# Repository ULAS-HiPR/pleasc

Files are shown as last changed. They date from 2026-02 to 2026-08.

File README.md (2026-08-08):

# Pléasc

Pléasc is the recovery-deployment node in [Ogma](https://sean-osullivan.com/projects/ogma/), the University of Limerick Aeronautics Society's modular avionics stack for high-powered rocketry.

## Role

- Monitors continuity on four deployment channels.
- Controls four recovery outputs from an STM32F072.
- Uses guarded arm and fire commands over the 500 kbit/s CAN bus.
- Keeps recovery outputs in defined safe states unless the complete command path is valid.

## Repository

- `hardware/` - KiCad design and manufacturing outputs.
- `firmware/` - embedded firmware, continuity/deployment probes, and tests.

## Status

Rev 1 firmware and hardware bring-up continue on [`ogma/flight-hardening`](https://github.com/ULAS-HiPR/pleasc/tree/ogma/flight-hardening). Release-candidate firmware builds and software tests pass, but hardware-in-the-loop validation is still underway. Pléasc is not yet flight-proven.

## Manufacturing support

Rev 1 PCB fabrication was sponsored through [EasyEDA Education](https://easyeda.com/education) and manufactured by [JLCPCB](https://jlcpcb.com/). The board was designed in KiCad and imported into EasyEDA Pro for the sponsorship and manufacturing workflow.

## More information

See the [Ogma project write-up](https://sean-osullivan.com/projects/ogma/) for the complete stack, bring-up work, and current status.

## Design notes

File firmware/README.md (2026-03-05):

# Lamh

Lamh is for any active control like airbrakes or canards. It will control servos.

## Set-Up

```bash
git clone git@github.com:ULAS-HiPR/pleasc.git
cd lamh
git submodule update --init --recursive
```

## Libraries used:

### From Braiteoiri:

- Servo
- LED

### From Comheadan:

- CAN
- PWM

### Other:

- FreeRTOS

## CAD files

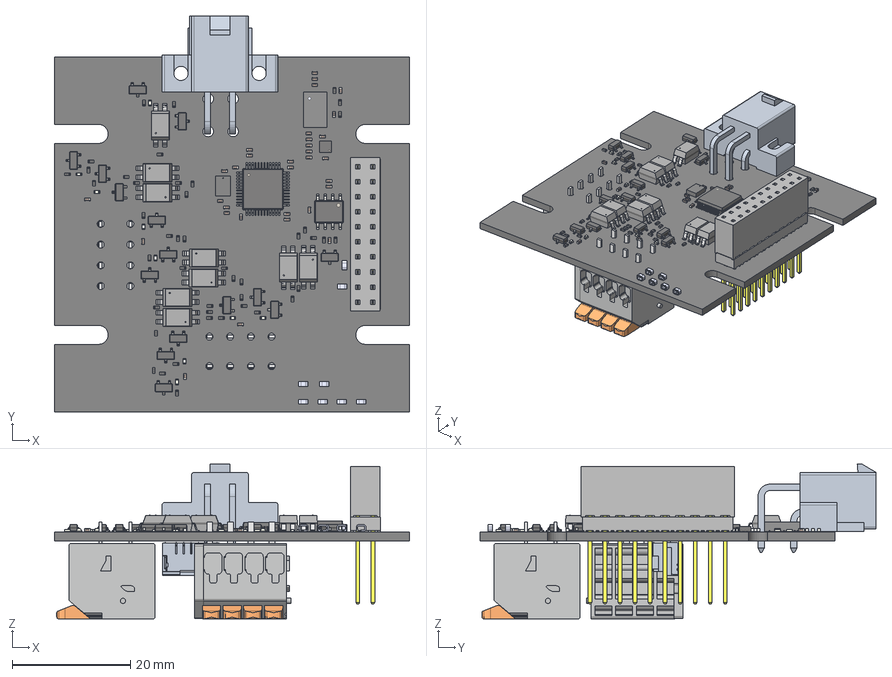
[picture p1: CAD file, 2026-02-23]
hardware/Pleasc.step
60.0 x 66.9 x 26.1 mm
C_0402_1005Metric x 32
S2761-46R x 8
R_0402_1005Metric x 44
SOT-23 x 15
LTV-817S x 9
LED_0402_1005Metric x 9
SOIC-8_3.9x4.9mm_P1.27mm
MPM3650CGQW
WSON-6-1EP_2x2mm_P0.65mm_EP1x1.6mm
ESQ-110-14-G-D-LL_socket
ESQ-110-14-G-D-LL_pins
ESQ-110-14-G-D-LL2_pins
ESQ-110-14-G-D-LL_bpins
LQFP-48_7x7mm_P0.5mm
XTAL_NX3225GD-8MHZ-STD-CRA-3_NDK
Pleasc_PCB

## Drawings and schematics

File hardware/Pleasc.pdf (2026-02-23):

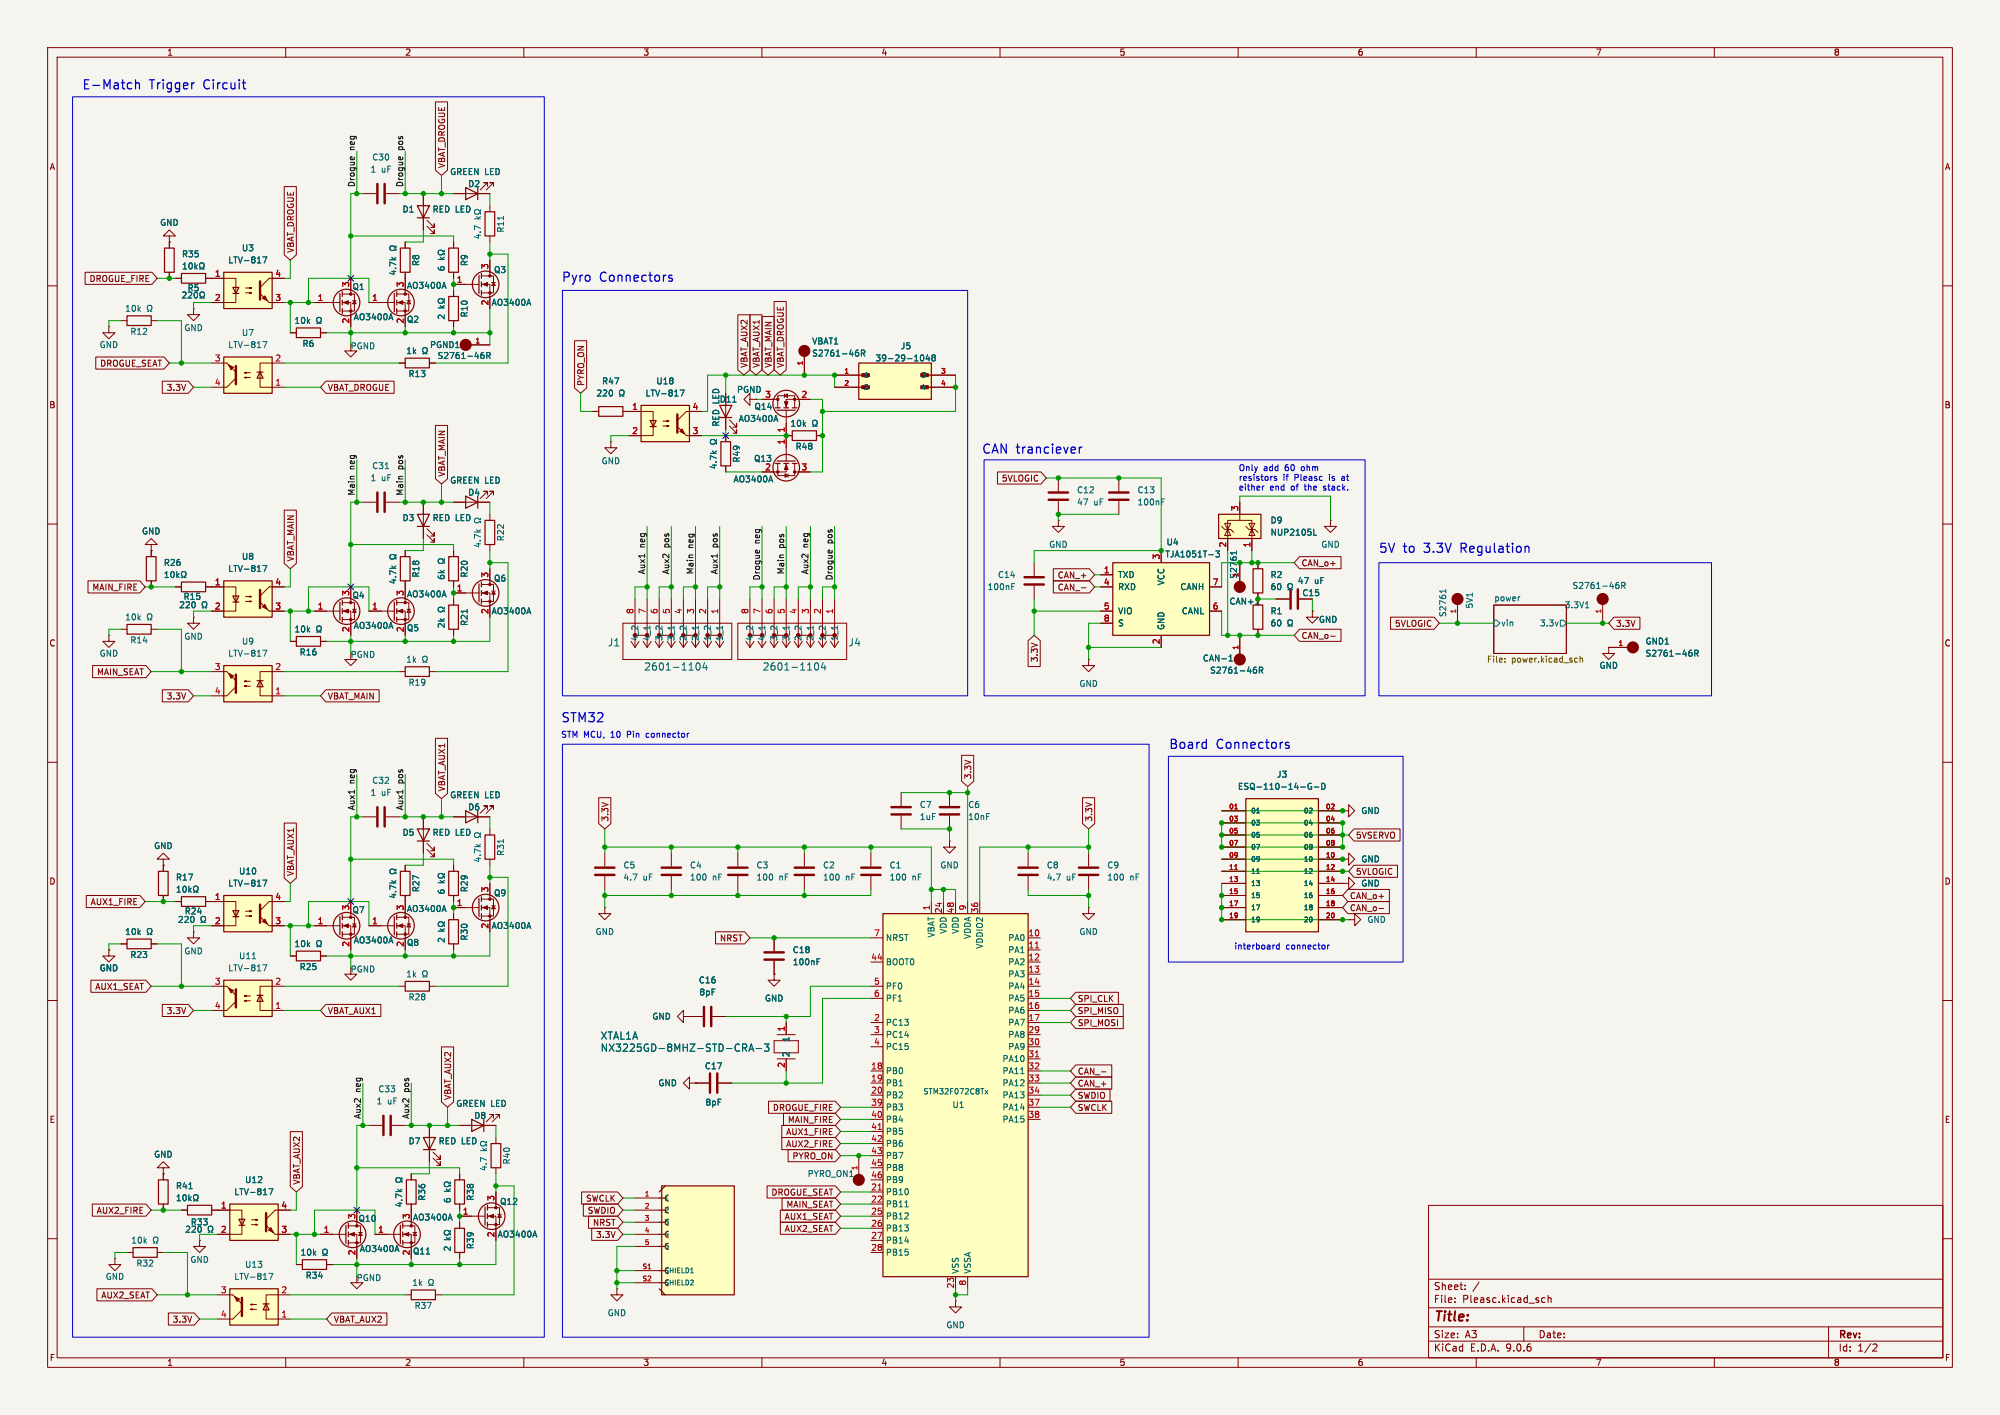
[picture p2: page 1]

CAN tranciever STM MCU, 10 Pin connector STM32

1 VDD 24 VDD 48 VSS 23 VDDA

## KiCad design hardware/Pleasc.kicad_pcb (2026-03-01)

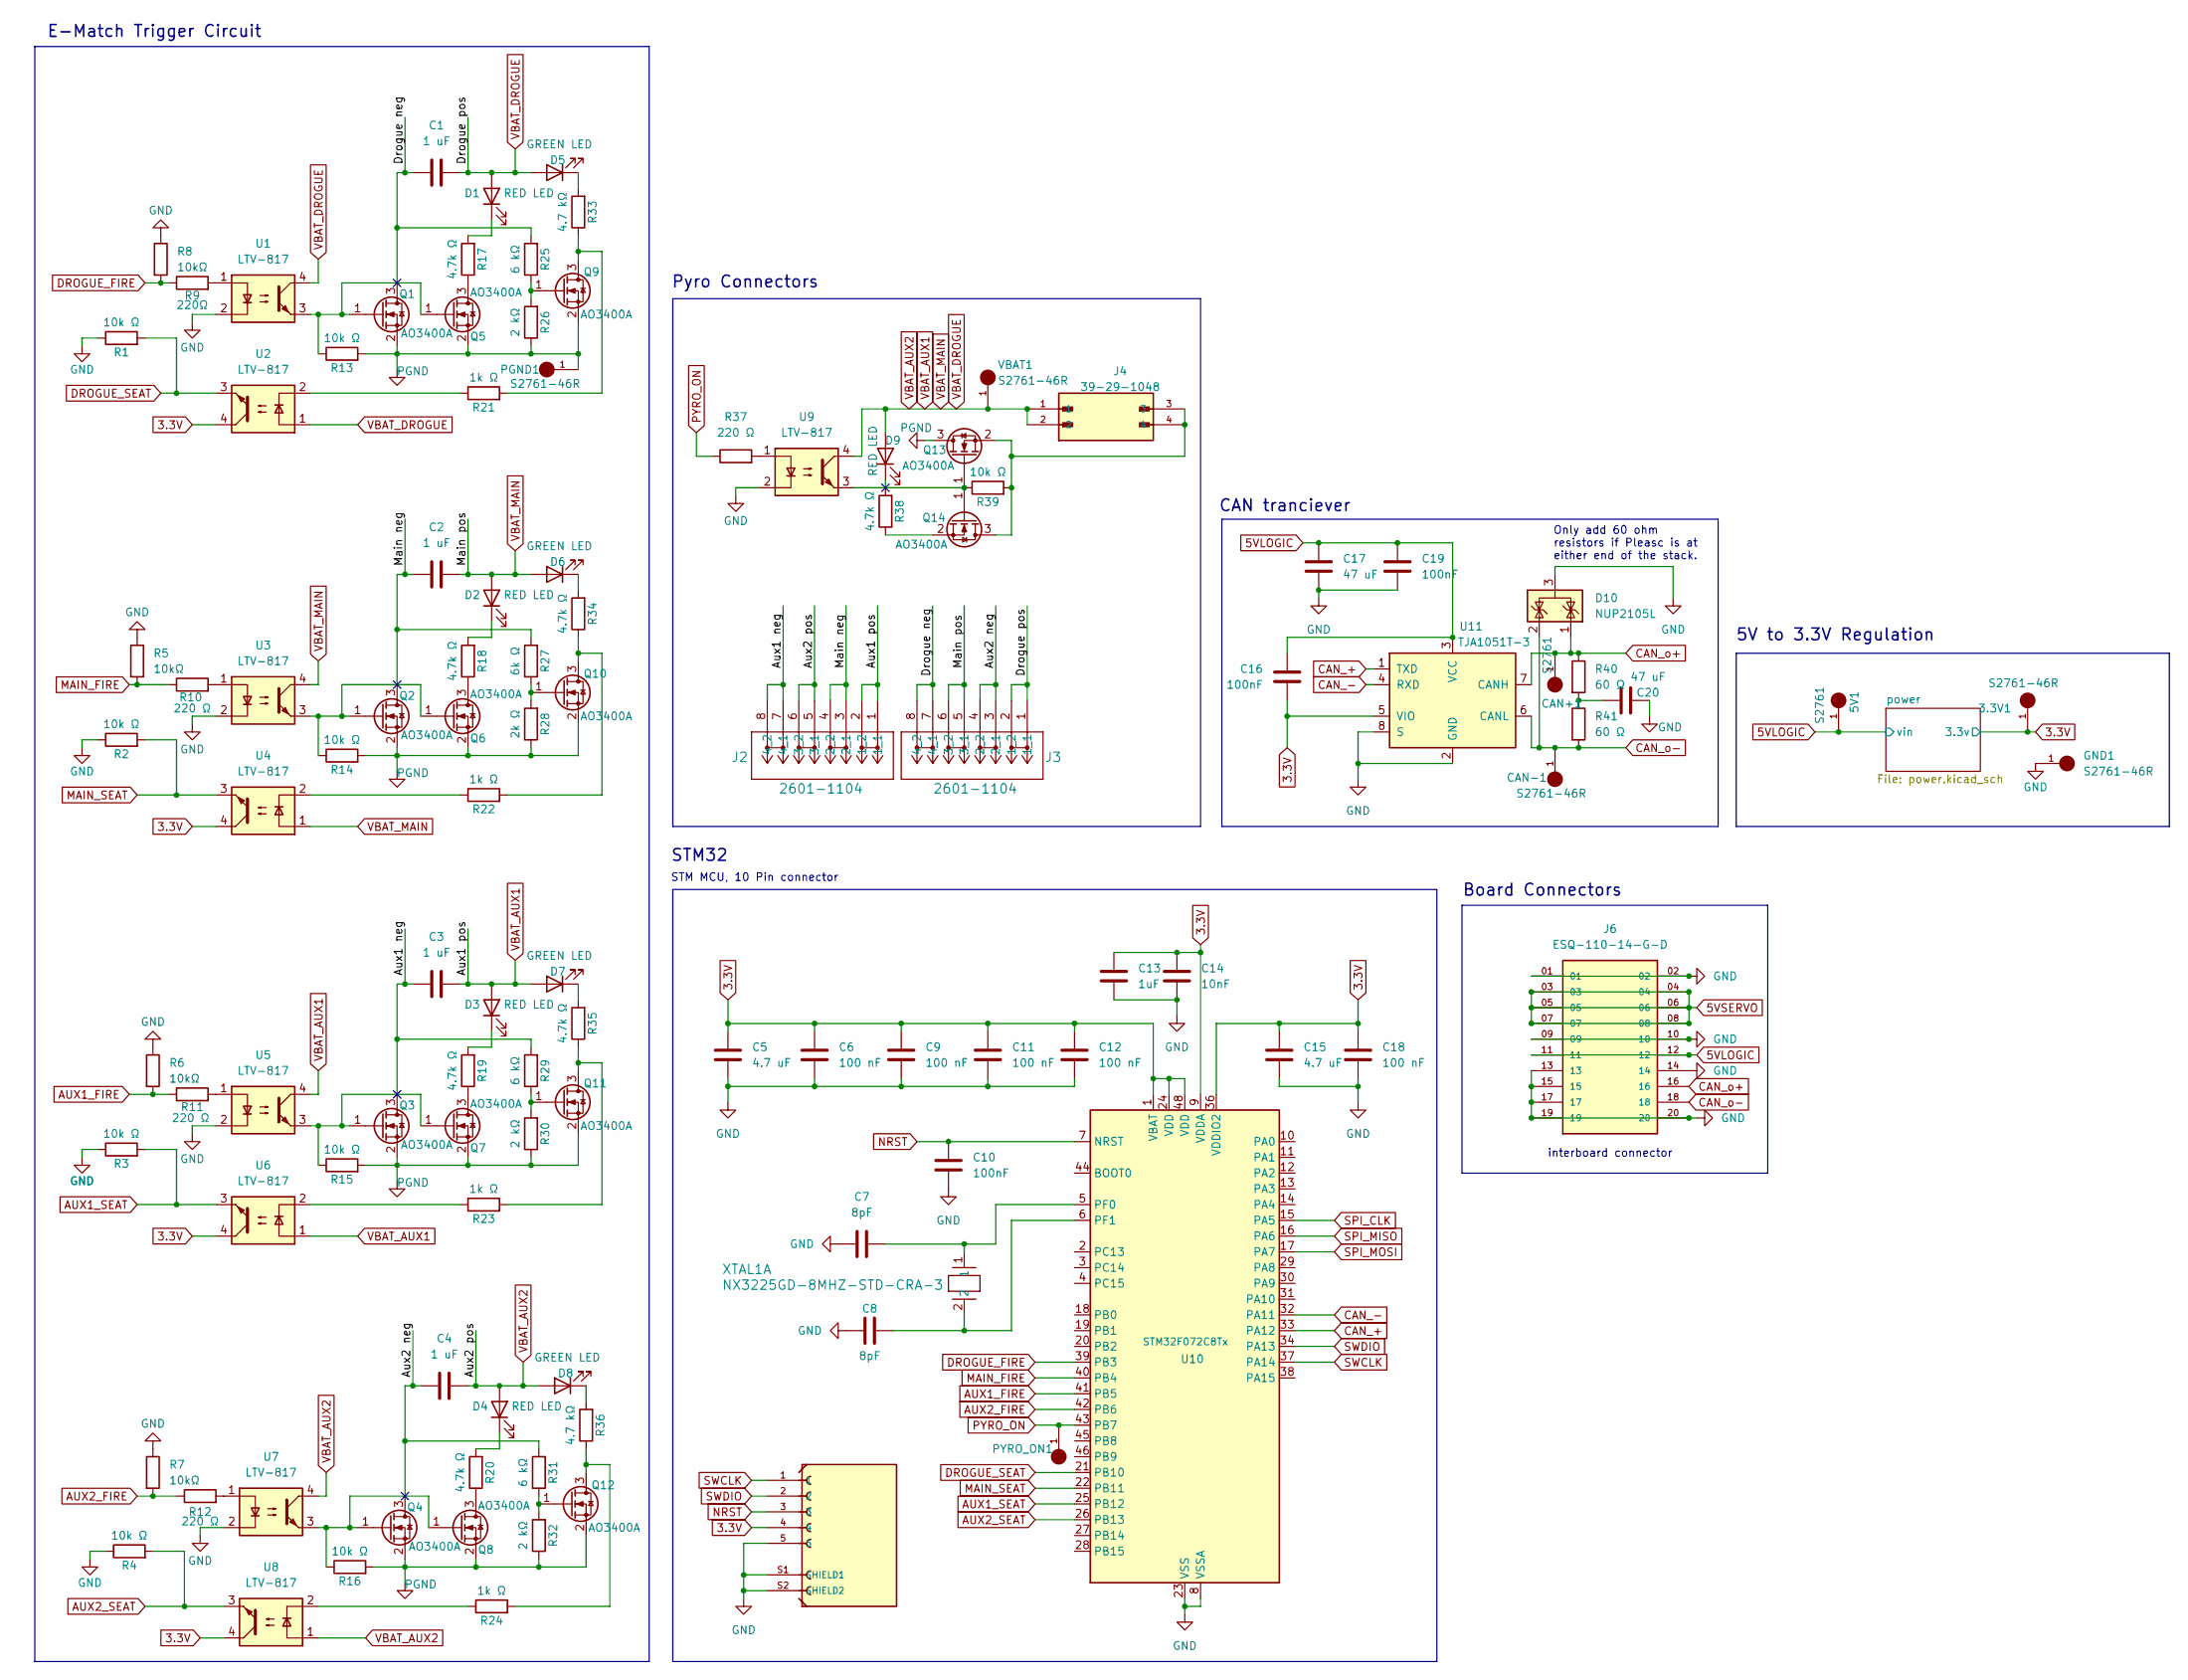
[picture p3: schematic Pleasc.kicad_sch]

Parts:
3.3V1: S2761-46R; HARWIN_S2761-46R; PARTREV 1
5V1: S2761; HARWIN_S2761-46R; PARTREV 1
C1, C2, C3, C4: 1 uF; C_0402_1005Metric
C5, C15: 4.7 uF; C_0402_1005Metric
C6, C9, C11, C12, C18: 100 nF; C_0402_1005Metric
C7, C8: 8pF; C_0402_1005Metric
C10, C16, C19: 100nF; C_0402_1005Metric
C13: 1uF; C_0402_1005Metric
C14: 10nF; C_0402_1005Metric
C17, C20: 47 uF; C_0402_1005Metric
CAN+1: S2761; HARWIN_S2761-46R; PARTREV 1
CAN-1: S2761-46R; HARWIN_S2761-46R; PARTREV 1
D1, D2, D3, D4, D9: RED LED; LED_0402_1005Metric
D5, D6, D7, D8: GREEN LED; LED_0402_1005Metric
D10: NUP2105L; SOT-23
GND1: S2761-46R; HARWIN_S2761-46R; PARTREV 1
J1: 5023860570; MOLEX_5023860570; PARTREV F
J2, J3: 2601-1104; CONN4_2601-1104_WAG
J4: 39-29-1048; MOLEX_39-29-1048
J6: ESQ-110-14-G-D; SAMTEC_ESQ-110-14-G-D; PARTREV NA
PGND1: S2761-46R; HARWIN_S2761-46R; PARTREV 1
PYRO_ON1: S2761-46R; HARWIN_S2761-46R; PARTREV 1
Q1, Q2, Q3, Q4, Q5, Q6, Q7, Q8, Q9, Q10, Q11, Q12, Q13, Q14: AO3400A; SOT-23
R1, R2, R3, R4, R13, R14, R15, R16, R39: 10k Ω; R_0402_1005Metric
R5, R6, R7, R8: 10kΩ; R_0402_1005Metric
R9: 220Ω; R_0402_1005Metric
R10, R11, R12, R37: 220 Ω; R_0402_1005Metric
R17, R18, R19, R20, R34, R35, R38: 4.7k Ω; R_0402_1005Metric
R21, R22, R23, R24: 1k Ω; R_0402_1005Metric
R25, R29, R31: 6 kΩ; R_0402_1005Metric
R26, R30, R32: 2 kΩ; R_0402_1005Metric
R27: 6k Ω; R_0402_1005Metric
R28: 2k Ω; R_0402_1005Metric
R33, R36: 4.7 kΩ; R_0402_1005Metric
R40, R41: 60 Ω; R_0402_1005Metric
U1, U2, U3, U4, U5, U6, U7, U8, U9: LTV-817; SO4_TOS
U10: STM32F072C8Tx; LQFP-48_7x7mm_P0.5mm
U11: TJA1051T-3; SOIC-8_3.9x4.9mm_P1.27mm
VBAT1: S2761-46R; HARWIN_S2761-46R; PARTREV 1
XTAL1: NX3225GD-8MHZ-STD-CRA-3; XTAL_NX3225GD-8MHZ-STD-CRA-3_NDK

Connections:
3.3V: 3.3V1.1, C5.1, C6.1, C9.1, C11.1, C12.1, C13.1, C14.1, C15.1, C16.1, C18.1, J1.4, U2.4, U4.4, U6.4, U8.4, U10.1 (VBAT), U10.9 (VDDA), U10.24 (VDD), U10.36 (VDDIO2), U10.48 (VDD), U11.5 (VIO); also elsewhere on the board
5VLOGIC: 5V1.1, C16.2, C17.1, C19.1, J6.11, J6.12, U11.3 (VCC); also elsewhere on the board
5VSERVO: J6.03, J6.04, J6.05, J6.06, J6.07, J6.08
/Aux1 neg: C3.2, J2.7 (4_1), J2.8 (4_2), Q3.3 (D), R29.2
/Aux2 neg: C4.2, J3.3 (2_1), J3.4 (2_2), Q4.3 (D), R31.2
/Drogue neg: C1.2, J3.7 (4_1), J3.8 (4_2), Q1.3 (D), R25.2
/Main neg: C2.2, J2.3 (2_1), J2.4 (2_2), Q2.3 (D), R27.2
AUX1_FIRE: R6.2, R11.1, U10.41 (PB5)
AUX1_SEAT: R3.2, U6.3, U10.25 (PB12)
AUX2_FIRE: R7.2, R12.1, U10.42 (PB6)
AUX2_SEAT: R4.2, U8.3, U10.26 (PB13)
CAN_+: U10.33 (PA12), U11.1 (TXD)
CAN_-: U10.32 (PA11), U11.4 (RXD)
CAN_o+: CAN+1.1, D10.1 (K), J6.16, R40.1, U11.7 (CANH)
CAN_o-: CAN-1.1, D10.2 (K), J6.18, R41.2, U11.6 (CANL)
DROGUE_FIRE: R8.2, R9.1, U10.39 (PB3)
DROGUE_SEAT: R1.2, U2.3, U10.21 (PB10)
GND: C5.2, C6.2, C7.1, C8.1, C9.2, C10.2, C11.2, C12.2, C13.2, C14.2, C15.2, C17.2, C18.2, C19.2, C20.2, D10.3 (A), GND1.1, J1.5, J1.S1 (SHIELD1), J1.S2 (SHIELD2), J6.01, J6.02, J6.09, J6.10, J6.13, J6.14, J6.15, J6.17, J6.19, J6.20, R1.1, R2.1, R3.1, R4.1, R5.1, R6.1, R7.1, R8.1, U1.2, U3.2, U5.2, U7.2, U9.2, U10.8 (VSSA), U10.23 (VSS), U10.35 (VSS), U10.47 (VSS), U11.2 (GND), U11.8 (S); also elsewhere on the board
MAIN_FIRE: R5.2, R10.1, U10.40 (PB4)
MAIN_SEAT: R2.2, U4.3, U10.22 (PB11)
NRST: C10.1, J1.3, U10.7 (NRST)
unnamed: C20.1, R40.2, R41.1
unnamed: D1.1 (K), R17.2
unnamed: D2.1 (K), R18.2
unnamed: D3.1 (K), R19.2
unnamed: D4.1 (K), R20.2
unnamed: D5.1 (K), R33.2
unnamed: D6.1 (K), R34.2
unnamed: D7.1 (K), R35.2
unnamed: D8.1 (K), R36.2
unnamed: Q1.1 (G), Q5.1 (G), R13.1, U1.3
unnamed: Q2.1 (G), Q6.1 (G), R14.1, U3.3
unnamed: Q3.1 (G), Q7.1 (G), R15.1, U5.3
unnamed: Q4.1 (G), Q8.1 (G), R16.1, U7.3
unnamed: Q5.3 (D), R17.1
unnamed: Q6.3 (D), R18.1
unnamed: Q7.3 (D), R19.1
unnamed: Q8.3 (D), R20.1
unnamed: Q9.3 (D), R21.2, R33.1
unnamed: Q9.1 (G), R25.1, R26.2
unnamed: Q10.3 (D), R22.2, R34.1
unnamed: Q10.1 (G), R27.1, R28.2
unnamed: Q11.3 (D), R23.2, R35.1
unnamed: Q11.1 (G), R29.1, R30.2
unnamed: Q12.3 (D), R24.2, R36.1
unnamed: Q12.1 (G), R31.1, R32.2
unnamed: Q13.1 (G), Q14.1 (G), R39.1, U9.3
unnamed: J4.3, J4.4, Q13.2 (S), Q14.3 (D), R39.2
unnamed: Q14.2 (S), R38.1
unnamed: R9.2, U1.1
unnamed: R10.2, U3.1
unnamed: R11.2, U5.1
unnamed: R12.2, U7.1
unnamed: R21.1, U2.2
unnamed: R22.1, U4.2
unnamed: R23.1, U6.2
unnamed: R24.1, U8.2
unnamed: R37.2, U9.1
unnamed: C7.2, U10.5 (PF0), XTAL1.1
unnamed: C8.2, U10.6 (PF1), XTAL1.2
PGND: PGND1.1, Q1.2 (S), Q2.2 (S), Q3.2 (S), Q4.2 (S), Q5.2 (S), Q6.2 (S), Q7.2 (S), Q8.2 (S), Q9.2 (S), Q10.2 (S), Q11.2 (S), Q12.2 (S), Q13.3 (D), R13.2, R14.2, R15.2, R16.2, R26.1, R28.1, R30.1, R32.1
PYRO_ON: PYRO_ON1.1, R37.1, U10.43 (PB7)
SPI_CLK: U10.15 (PA5)
SPI_MISO: U10.16 (PA6)
SPI_MOSI: U10.17 (PA7)
SWCLK: J1.1, U10.37 (PA14)
SWDIO: J1.2, U10.34 (PA13)
VBAT_AUX1: C1.1, C2.1, C3.1, C4.1, D1.2 (A), D2.2 (A), D3.2 (A), D4.2 (A), D5.2 (A), D6.2 (A), D7.2 (A), D8.2 (A), D9.2 (A), J2.1 (1_1), J2.2 (1_2), J2.5 (3_1), J2.6 (3_2), J3.1 (1_1), J3.2 (1_2), J3.5 (3_1), J3.6 (3_2), J4.1, J4.2, U1.4, U2.1, U3.4, U4.1, U5.4, U6.1, U7.4, U8.1, U9.4, VBAT1.1

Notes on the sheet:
5V to 3.3V Regulation
STM32
CAN tranciever
E-Match Trigger Circuit
STM MCU, 10 Pin connector
Pyro Connectors
interboard connector
Board Connectors
Only add 60 ohm resistors if Pleasc is at either end of the stack.

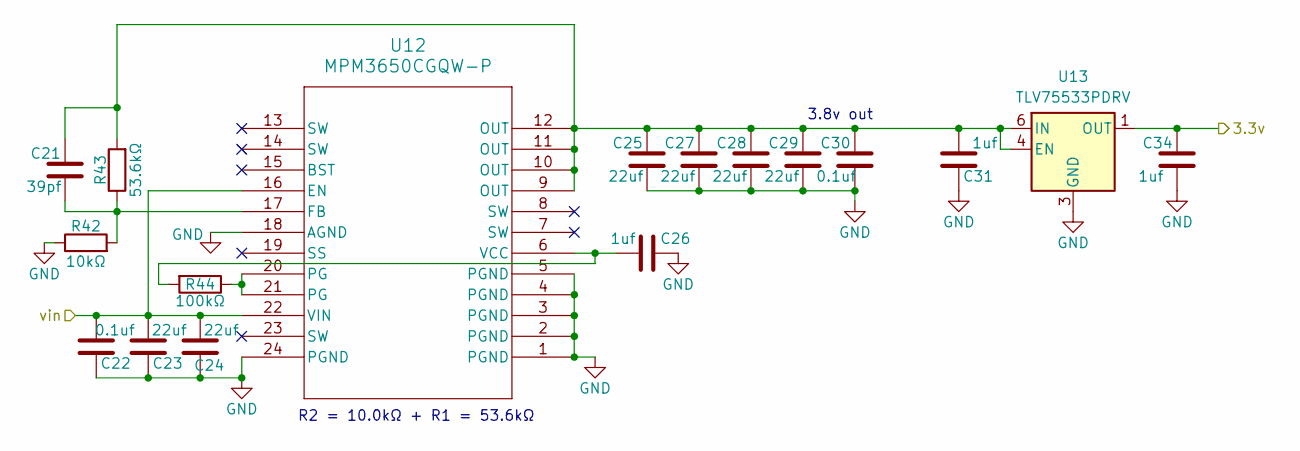
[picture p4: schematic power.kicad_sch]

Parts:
C21: 39pf; C_0402_1005Metric
C22, C30: 0.1uf; C_0402_1005Metric
C23, C24, C25, C27, C28, C29: 22uf; C_0402_1005Metric
C26, C31, C34: 1uf; C_0402_1005Metric
R42: 10kΩ; R_0402_1005Metric
R43: 53.6kΩ; R_0402_1005Metric
R44: 100kΩ; R_0402_1005Metric
U12: MPM3650CGQW-P; QFN-24_MPM3650_MNP
U13: TLV75533PDRV; WSON-6-1EP_2x2mm_P0.65mm_EP1x1.6mm

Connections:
3.3V: C34.1, U13.1 (OUT); also elsewhere on the board
5VLOGIC: C22.2, C23.2, C24.2, U12.16 (EN), U12.22 (VIN); also elsewhere on the board
GND: C22.1, C23.1, C24.1, C25.2, C26.1, C27.2, C28.2, C29.2, C30.2, C31.1, C34.2, R42.1, U12.1 (PGND), U12.2 (PGND), U12.3 (PGND), U12.4 (PGND), U12.5 (PGND), U12.18 (AGND), U12.24 (PGND), U13.3 (GND), U13.7 (GND); also elsewhere on the board
unnamed: R44.1, U12.20 (PG), U12.21 (PG)
unnamed: C21.2, R42.2, R43.1, U12.17 (FB)
unnamed: C26.2, R44.2, U12.6 (VCC)
unnamed: C21.1, C25.1, C27.1, C28.1, C29.1, C30.1, C31.2, R43.2, U12.9 (OUT), U12.10 (OUT), U12.11 (OUT), U12.12 (OUT), U13.4 (EN), U13.6 (IN)

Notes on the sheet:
3.8v out
R2 = 10.0kΩ + R1 = 53.6kΩ

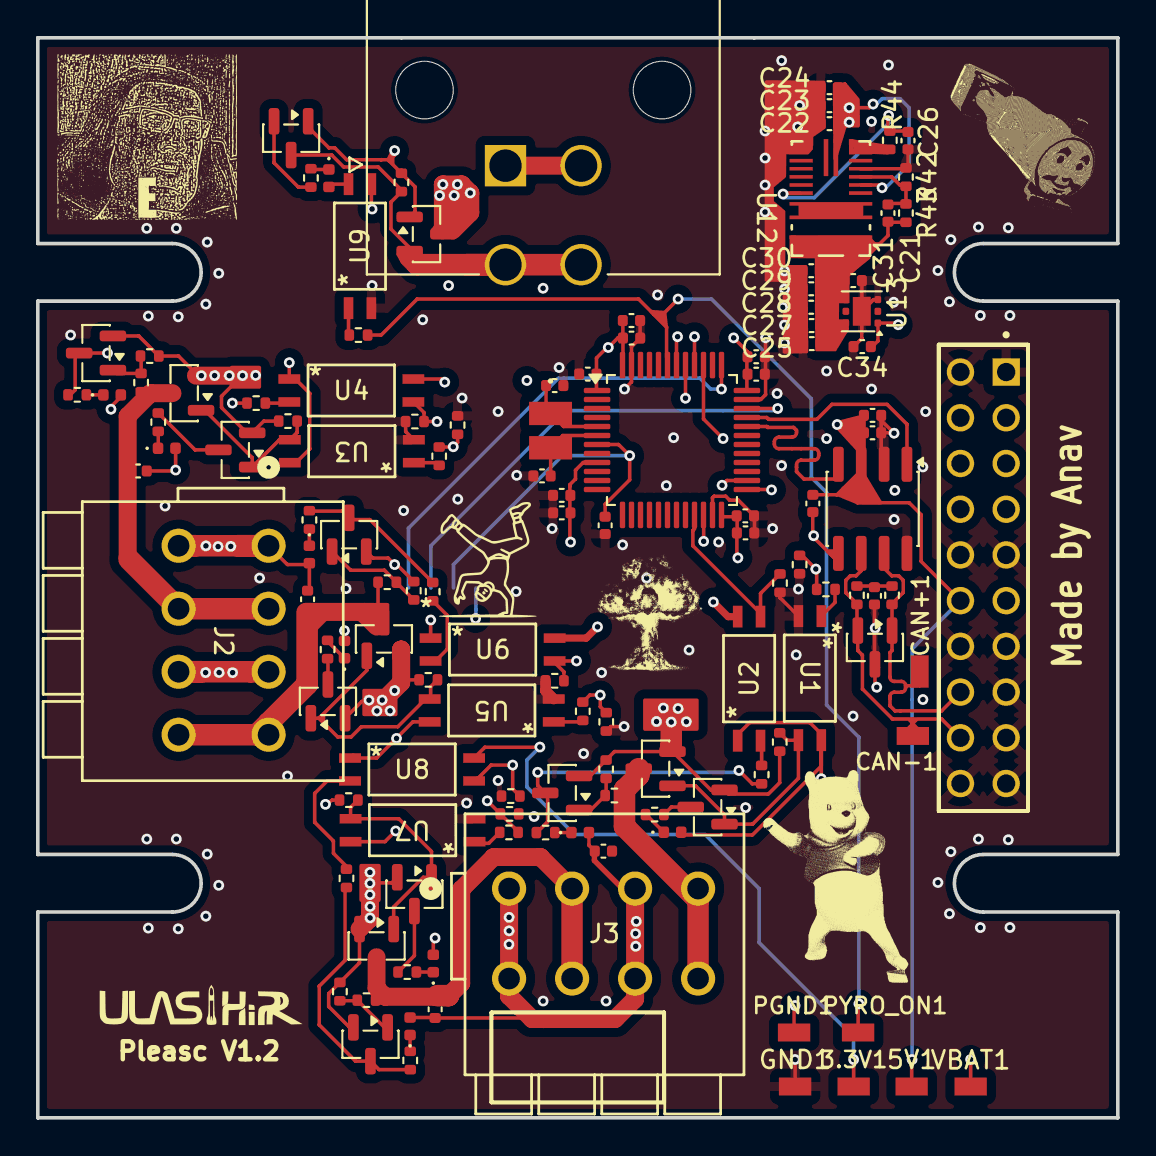
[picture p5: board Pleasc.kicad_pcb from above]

Board: 6 copper layers, 60.0 x 60.0 mm, 127 parts (1 on the bottom side), 69 nets.

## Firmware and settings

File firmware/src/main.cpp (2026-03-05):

#if F4
#include "stm32f4xx_hal.h"
#include "platform/stm_f4.h"
#endif
#include "cmsis_os.h"

#include <data.h>
#include <sensor.h>

#include <I2C/I2C_STM.h>
#include <SPI/SPI_STM.h>

#include "tasks/default.h"


void SystemClock_Config(void);
void Error_Handler(void);


int main(void)
{
  HAL_Init();
  SystemClock_Config();
  osKernelInitialize();

  
  static task::Default default_task; 
  default_task.run();

  
  osKernelStart();
  // never get here 
  while (1)
  {
    HAL_Delay(1000);
  }
}



/**
  * @brief System Clock Configuration
  * @retval None
  */
void SystemClock_Config(void)
{
  RCC_OscInitTypeDef RCC_OscInitStruct = {0};
  RCC_ClkInitTypeDef RCC_ClkInitStruct = {0};

  /** Configure the main internal regulator output voltage
  */
  __HAL_RCC_PWR_CLK_ENABLE();
  __HAL_PWR_VOLTAGESCALING_CONFIG(PWR_REGULATOR_VOLTAGE_SCALE1);

  /** Initializes the RCC Oscillators according to the specified parameters
  * in the RCC_OscInitTypeDef structure.
  */
  RCC_OscInitStruct.OscillatorType = RCC_OSCILLATORTYPE_HSI;
  RCC_OscInitStruct.HSIState = RCC_HSI_ON;
  RCC_OscInitStruct.HSICalibrationValue = RCC_HSICALIBRATION_DEFAULT;
  RCC_OscInitStruct.PLL.PLLState = RCC_PLL_ON;
  RCC_OscInitStruct.PLL.PLLSource = RCC_PLLSOURCE_HSI;
  RCC_OscInitStruct.PLL.PLLM = 16;
  RCC_OscInitStruct.PLL.PLLN = 336;
  RCC_OscInitStruct.PLL.PLLP = RCC_PLLP_DIV4;
  RCC_OscInitStruct.PLL.PLLQ = 4;
  if (HAL_RCC_OscConfig(&RCC_OscInitStruct) != HAL_OK)
  {
    Error_Handler();
  }

  /** Initializes the CPU, AHB and APB buses clocks
  */
  RCC_ClkInitStruct.ClockType = RCC_CLOCKTYPE_HCLK|RCC_CLOCKTYPE_SYSCLK
                              |RCC_CLOCKTYPE_PCLK1|RCC_CLOCKTYPE_PCLK2;
  RCC_ClkInitStruct.SYSCLKSource = RCC_SYSCLKSOURCE_PLLCLK;
  RCC_ClkInitStruct.AHBCLKDivider = RCC_SYSCLK_DIV1;
  RCC_ClkInitStruct.APB1CLKDivider = RCC_HCLK_DIV2;
  RCC_ClkInitStruct.APB2CLKDivider = RCC_HCLK_DIV1;

  if (HAL_RCC_ClockConfig(&RCC_ClkInitStruct, FLASH_LATENCY_2) != HAL_OK)
  {
    Error_Handler();
  }
}

void Error_Handler(void)
{
  __disable_irq();
  while (1)
  {
    // stay here
  }
}

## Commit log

2026-01-27 Schematic complete, components layed out on the PCB
    [Pleasc.kicad_pcb, Pleasc.kicad_sch]
2026-01-29 All 4 Pyros circuits routed
    [Pleasc.kicad_pcb, Pleasc.kicad_sch]
2026-01-31 added can crystal
    [Pleasc.kicad_sch]
2026-02-09 Version 1.2
    [Pleasc.kicad_sch]
2026-02-22 ready for review
    [Pleasc.kicad_pcb, Pleasc.kicad_sch]
2026-02-23 ready for review the twost
    [Pleasc.kicad_pcb, Pleasc.step, power.kicad_sch]
2026-02-27 ready to go, nearly
    [Pleasc-B_Cu.gbr, Pleasc-B_Mask.gbr, Pleasc-B_Paste.gbr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]
2026-03-01 ready 2 order
    [Pleasc-B_Cu.gbr, Pleasc-B_Mask.gbr, Pleasc-B_Paste.gbr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]
